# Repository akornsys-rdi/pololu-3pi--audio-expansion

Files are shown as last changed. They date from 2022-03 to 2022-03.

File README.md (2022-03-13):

# Pololu 3PI+ Audio Expansion API

Expansion board to provide audio playback for Pololu 3pi+ 32U4 Robot

## System interconnection diagram

            ┌──────┐   ┌──────┐         D    ┌───┐
            │ USB  │   │ USB  │       ┌──────┤RX │
            │SUBSYS│   │SUBSYS│       │      │ANT│
            ├──────┤   ├──────┤       ▼      └───┘
            ├──────┤ B ├──────┤   ┌──────┐
    ┌───┐   │      │◄──┤      │   │      │   ┌───┐
    │BAT├──►│ 32U4 │   │ SAMD │◄─►┤ TINY ├──►│RGB│
    │LVL│ A │      ├──►│      │ E │      │ D │LED│
    └───┘   ├──────┤ C ├──────┤   └──────┘   └───┘
            ├──────┤   ├──────┤       ▲
            │ROBOT │   │AUDIO │       │      ┌───┐
            │SUBSYS│   │SUBSYS│       └──────┤ID │
            └──────┘   └──────┘         A    │POT│
                                             └───┘
    COMMUNICATION:
    A -> ANALOG             B -> SERIAL DOWNLINK
    C -> SERIAL UPLINK      D -> DIGITAL PROTOCOL
    E -> DIGITAL INTERLINK

## Communication protocols

- Battery reading by analog reading of `A1` of the **ATmega32U4**, the `readBatteryMillivolts()` function (implemented by the Pololu library) provides this functionality.
- Reading the identifier selection potentiometer by analog reading of `A2` from the **ATtiny85**, the `readIdPot()` function (to be implemented in code) provides this functionality.
- Bidirectional communication between **ATmega32U4** and **ATSAMD21** via serial protocol with level shifting at 115200bps. The `Serial1` port is at the **ATmega32U4** end, while the `Serial` port is at the **ATSAMD21** end.
- Reading of the 433MHz radio receiver in 24bit protocol. Realized by the `rc-switch` library (fork).
- WS2812B type RGB LED writing. Realized by the `Adafruit NeoPixel` library.
- Communication primarily one-way from the **ATtiny85** to the **ATSAMD21**. The line level determines what has been received via the radio, leaving the line in high impedance (with pulldown) until the first reception. At startup, different pulses are generated to check the initial status and send the identifier (see corresponding sections).

## Software versions

**ATmega32U4**
- IDE: Arduino IDE 1.8.19
- Board: [Pololu A-Star Boards](https://github.com/pololu/a-star) 4.0.2 by Pololu
- Libraries: 
  + [Pololu3piPlus32U4](https://github.com/pololu/pololu-3pi-plus-32u4-arduino-library) 1.1.2 by Pololu
    * [FastGPIO](https://github.com/pololu/fastgpio-arduino) 2.1.0 by Pololu
    * [USBPause](https://github.com/pololu/usb-pause-arduino) 2.0.0 by Pololu
    * [Pushbutton](https://github.com/pololu/pushbutton-arduino) 2.0.0 by Pololu
    * [PololuBuzzer](https://github.com/pololu/pololu-buzzer-arduino) 1.2.0 by Pololu
    * [PololuHD44780](https://github.com/pololu/pololu-hd44780-arduino) 2.0.0 by Pololu
    * [PololuOLED](https://github.com/pololu/pololu-oled) 2.0.0 by Pololu
    * [PololuMenu](https://github.com/pololu/pololu-menu-arduino) 2.0.0 by Pololu
  + [TimerThree](https://playground.arduino.cc/Code/Timer1/) 1.1.0 by Jesse Tane, Jérôme Despatis, Michael Polli, Dan Clemens, Paul Stoffregen
  + [movingAvg](https://github.com/JChristensen/movingAvg) 2.3.1 by Jack Christensen

**ATSAMD21**
- IDE: Arduino IDE 1.8.19
- Board: Arduino SAMD Boards (32-bits ARM Cortex-M0+) 1.8.7 by Arduino
- Libraries:
  + [Arduino Sound](https://www.arduino.cc/en/Reference/ArduinoSound) 0.2.1 by Arduino
  + [SD](https://www.arduino.cc/en/Reference/SD) 1.2.3 by Arduino
  + [SDConfig](https://www.arduino.cc/reference/en/libraries/sdconfig/) 1.1.0 by Claus Mancini

**ATtiny85**
- IDE: Arduino IDE 1.8.19
- Board: [attiny](https://github.com/damellis/attiny) 1.0.2 by David A. Mellis
- Libreries: 
  + [Adafruit NeoPixel](https://github.com/adafruit/Adafruit_NeoPixel) 1.1.8 by Adafruit
  + [rc-switch](https://github.com/luelista/rc-switch/tree/feature-pcint-rebased) 2.6.2 by Mira Weller (fork).
    * [PinChangeInterrupt](https://github.com/NicoHood/PinChangeInterrupt) 1.2.9 by NicoHood
  + [ATtinySerialOut](https://github.com/ArminJo/ATtinySerialOut) 1.1.0 by Armin Joachimsmeyer

## General information

All **ATtiny85**, **ATSAMD21** and **ATmega32U4** firmware must share common values in the `N_ROBOTS` constant with the value of the maximum number of robots running simultaneously.

## Initial check

The **ATSAMD21** shall perform an initial check at startup, where it will check for the existence and correct access to the SD card, as well as that there is at least one valid audio of each required type. Hardware checks may also be performed. If any of these checks are not correct, the **ATSAMD21** will send the command `#` to the **ATmega32U4**, flash the user LED and, if available, attempt to play a special audio to indicate this circumstance. After this it will latch, ceasing to perform any other functionality until a power cycle is performed.

If the check is successful, it will send the `%` command, and will play, if available, an OK check audio. In the case of having the special audio of check ok, the command of this circumstance will be sent at the end of the reproduction of this audio. Once the initial check has been performed, the system will be able to perform the other functionalities explained in this document.

During the initial check at start-up of **ATSAMD21**, it will maintain the interlink line with **ATtiny85** at high level, thus indicating that it is present and that it is in the process of being checked. As soon as the initial check process is finished, this line will be set low and control of it will be given to the identifier assignment routine.

The **ATtiny85** can set a timeout time waiting for this high level signal, which if it does not appear, it will be considered that communication between these two microcontrollers cannot be established.

If the `MAIN.CFG` file is available on the SD card, it will try to read from it new settings, which will replace the default settings.

The **ATmega32U4** can set a timeout time, after which the Audio Expansion board is considered not available or does not respond. The behavior in this scenario is not determined.

## Identifier assignment operation

The assignment of the identifier is performed at system startup, when the potentiometer that selects the identifier is read. This reading by the **ATtiny85** is processed and converted into a range between `0` and `N_ROBOTS - 1`. The resulting `identifier` is transmitted by a variable width pulse to the **ATSAMD21**. Each identifier is assigned a color on the RGB LED by dividing the color spectrum by the constant `N_ROBOTS` and multiplying the hue angle by `identifier`.

For the pulse indicating the assigned identifier, the **ATSAMD21** after having performed its initial check (being successful), will generate a low level pause on the interlink line of 750µs. After this, it will generate a first high level pulse of 50µs, thus indicating to the **ATtiny85** that it is ready to receive. 5µs later, the **ATtiny85** starts a pulse with a length of (360µs/`N_ROBOTS`)*`identifier`. After this pulse it waits another 25µs at low level before giving control of the line to the remote command routine.

During program execution, the **ATtiny85** periodically reads the potentiometer that selects the identifier for changes. If a change is produced, it displays the new color corresponding to the resulting identifier for three seconds. This functionality has priority in the use of the RGB LED. The new identifier does not replace the previous one, and a power cycle is required for the new identifier selected via the potentiometer to be assigned.

In the communication between the **ATmega32U4** and the **ATSAMD21**, the former can ask at any time for the current identifier, by sending an `@`. If the **ATSAMD21** has already received the identifier from the **ATtiny85**, it will send a character between the `A` and the `~`. Otherwise, it will respond with `@`, thus indicating that it is still unknown. If this circumstance occurs, the **ATmega32U4** must keep asking until it gets a valid answer.

## Remote command operation

The remote command operation allows to pause the robots, or to resume running. It is performed through a 433MHz command, and the command received is processed by the **ATtiny85**. This command is relayed to the **ATSAMD21** via the interlink line level. The **ATSAMD21** will send a command to the **ATmega32U4** with each change of this command. At startup, until the first reception, it should be considered to be in a paused state.

The **ATtiny85** microcontroller decodes the keystroke received from the control and considers whether it is a pause or run command. The interlink line will be set to low or high level respectively. The line remains in high impedance state (with pulldown) until the first command is received.

The RGB LED will blink with the color of the identifier if paused, and will remain fixed for five seconds from the moment of activation, before turning off. It will turn back on with each change of command, remaining in the previous state if a keystroke equal to the current command is repeated.

At the moment of a new change detected by the **ATSAMD21**, it will generate a command via serial port to the **ATmega32U4**. A `&` is sent in case of a run resume command, and a `$` in case of pause or standby. The **ATmega32U4** must receive the command. No response is required.

## Audio playback operation

The **ATmega32U4** shall be able to generate audio playback and end of playback command at any time after the initial check. The **ATSAMD21** shall receive the command and act accordingly. There are two playback commands, depending on their type. The `>` command will initiate playback of path audios (type A), which will be repeated indefinitely if it reaches its end. The `!` command will start the playback of collision audios (type B), which will be played only once. The path audios will stop on receipt of the `=` command.

In the event of path audio playback, the **ATSAMD21** shall choose a random audio file among those provided on the SD card of its type, and start the playback. Randomly, between 1 and 5 times, the same path audio shall be played in successive receptions of that command, after which another audio shall be randomly chosen again with the same strategy.

In the event of collision audio playback, the **ATSAMD21** shall choose a random audio file among those provided on the SD card of its type, and start its playback until the file reaches its end.

If a play command is received while an audio file is already playing, this command will be ignored as long as a special audio is not being played, in which case it will be added to the play queue and played when the special audio is finished.

On the path audio playback stop event, the current audio playback will be stopped, as long as it is of this type. This action will do nothing if a file is not playing or if the playback is of another type.

### File format

The WAVE file format must be PCM mono 16bit at 22050Hz, with extension `.wav`. Any other format cannot be played.

### File names

For path and collision audios, only those files that are consecutive from `000` will be considered.

| File name | Type | Description |
|---|---|---|
| `A000.WAV` - `A999.WAV` | Required | Interval of path audios |
| `B000.WAV` - `B999.WAV` | Required | Interval of collision audios  |
| `CHKOK.WAV` | Special  | Initial check ok indicator |
| `CHKKO.WAV` | Special  | Initial check error indicator |
| `LWBAT.WAV` | Special  | Low battery indicator |

Special audios are optional.

## Battery readout operation

The battery level must be constantly monitored, in order to stop the robot if the charge drops below the `LOW_BATT` threshold. This monitoring is done by the **ATmega32U4**, which must send a command to the **ATSAMD21** in case the battery voltage drops below this threshold, which is done by sending a `-` only at the time of detection. The current battery comparison is done using the average of the last readings against the threshold.

This event should cause a latching event, and should not be recoverable until power is cycled. The **ATSAMD21** will play a special audio (if available) once to indicate low battery. If an audio is playing at the time the low battery command is received, the special audio will be retained and played after the previous one has finished. This event does not affect the playback of other audios, which must be stopped if explicitly required by the **ATmega32U4**.

## Debugging and LED status indication

The different LEDs located on the different boards of each robot have a meaning that can help to understand the current behavior of the robot, as well as to detect possible failures and their cause.

| LED | Lighting mode | Current status | Notes |
|---|---|---|---|
| Green LED on main board | 1Hz blinking | Waiting for identifier of **ATSAMD21** | |
| Yellow LED on main board | Fixed | Motion after obstacle detection or timeout | |
| Red LED on main board | 2Hz blinking | Low battery | |
| Green, yellow and red LEDs on main board | 10Hz blinking | Error in initial check | All LEDs simultaneously |
| Red LED on Audio Expansion board | Fixed | Battery charging | With USB connected to Audio Expansion |
| Red LED on Audio Expansion board | Off | Battery charged | With USB connected to Audio Expansion |
| Orange LED on Audio Expansion board | 31Hz blinking | SD card not found | No SD card |
| Orange LED on Audio Expansion board | 31Hz blinking | Audio files not found or not valid | With SD card |
| Orange LED on Audio Expansion board | Fixed | Playing audio | |
| RGB LED on Audio Expansion board | Fixed any color | Identifying color assigned to the robot | Right at startup |
| RGB LED on Audio Expansion board | 15Hz white blinking | Awaiting communication with **ATSAMD21** | In start-up sequence |
| RGB LED on Audio Expansion board | Fixed pure green | Successful communication with **ATSAMD21** | In start-up sequence after white blinking, duration 500ms |
| RGB LED on Audio Expansion board | Fixed pure red | Unsuccessful communication with **ATSAMD21** | In start-up sequence after white blinking, duration 500ms |
| RGB LED on Audio Expansion board | 8Hz robot identifier blinking | Pause mode | After the start-up sequence |
| RGB LED on Audio Expansion board | Fixed robot identifier | Active mode | After the start-up sequence, duration 5s |
| RGB LED on Audio Expansion board | Off | Active mode | After the start-up sequence, after being fixed for 5s |
| RGB LED on Audio Expansion board | Fixed any color | Identification color selection | After the start-up sequence, moving the identifier selection potentiometer or up to 3 seconds later |

## Summary of uplink/downlink commands

| Source | Destination | Command | Description |
|---|---|---|---|
| **ATSAMD21** | **ATmega32U4** | `#` | Initial check error |
| **ATSAMD21** | **ATmega32U4** | `%` | Initial check ok |
| **ATmega32U4** | **ATSAMD21** | `@` | Identifier request |
| **ATSAMD21** | **ATmega32U4** | `@` | Answer: Unknown identifier |
| **ATSAMD21** | **ATmega32U4** | `A` - `~` | Answer: Identifier number |
| **ATSAMD21** | **ATmega32U4** | `$` | Set pause mode |
| **ATSAMD21** | **ATmega32U4** | `&` | Set active mode |
| **ATmega32U4** | **ATSAMD21** | `>` | Start of path audio playback |
| **ATmega32U4** | **ATSAMD21** | `=` | Stop audio path playback |
| **ATmega32U4** | **ATSAMD21** | `!` | Start of collision audio playback |
| **ATmega32U4** | **ATSAMD21** | `-` | Low battery indicator |

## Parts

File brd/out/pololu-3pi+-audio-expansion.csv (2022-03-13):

Reference | Value | Footprint | Datasheet | Manufacturer | Manufacturer Part Number
U1 | ATSAMD21G18A-AUT | Package_QFP:TQFP-48_7x7mm_P0.5mm | lib/datasheets/ATSAM-D21.pdf | Microchip | ATSAMD21G18A-AU
U2 | MAX98357 | Package_DFN_QFN:QFN-16-1EP_3x3mm_P0.5mm_EP1.45x1.45mm_ThermalVias | lib/datasheets/MAX98357.pdf | Maxim Integrated | MAX98357AETE+T
C12 | 220pF | Capacitor_SMD:C_0805_2012Metric |  | Samsung Electro-Mechanics | CL21C221JBANNNC
J2 | Micro_SD_Card | 5009010801:5009010801 | lib/datasheets/5009010801.pdf | Molex | 500901-0801
Q1 | 2N7002 | Package_TO_SOT_SMD:SOT-23 | lib/datasheets/NX7002AK.pdf | Nexperia | NX7002AKVL
R2 | 10k | Resistor_SMD:R_0805_2012Metric |  | Bourns | CR0805-JW-103ELF
R4 | 10k | Resistor_SMD:R_0805_2012Metric |  | Bourns | CR0805-JW-103ELF
Q2 | 2N7002 | Package_TO_SOT_SMD:SOT-23 | lib/datasheets/NX7002AK.pdf | Nexperia | NX7002AKVL
R3 | 10k | Resistor_SMD:R_0805_2012Metric |  | Bourns | CR0805-JW-103ELF
R5 | 10k | Resistor_SMD:R_0805_2012Metric |  | Bourns | CR0805-JW-103ELF
SW1 | RESET | Button_Switch_SMD:SW_Push_SPST_NO_Alps_SKRK | lib/datasheets/PTS636.pdf | C&K Switches | PTS636 SP43 SMTR LFS
Y1 | 32.768kHz | Crystal:Crystal_SMD_3215-2Pin_3.2x1.5mm | lib/datasheets/FC-135.pdf | Epson | FC-135 32.7680KA-A5
C1 | 22pF | Capacitor_SMD:C_0805_2012Metric |  | Samsung Electro-Mechanics | CL21C220JBANFNC
C2 | 22pF | Capacitor_SMD:C_0805_2012Metric |  | Samsung Electro-Mechanics | CL21C220JBANFNC
R1 | 220R | Resistor_SMD:R_0805_2012Metric |  | Bourns | CR0805-JW-221ELF
D1 | ORANGE | LED_SMD:LED_0805_2012Metric | lib/datasheets/LO-R976.pdf | Osram | LO R976-PS-1-0-20-R18
C10 | 100nF | Capacitor_SMD:C_0805_2012Metric |  | Kemet | C0805C104M5RACTU
L1 | Choke | Inductor_SMD:L_0805_2012Metric | lib/datasheets/BKPxxxxxxxx.pdf | Taiyo Yuden | BKP2125HS331-T
LS1 | Speaker | Connector_PinHeader_2.54mm:PinHeader_1x02_P2.54mm_Horizontal | lib/datasheets/10129379.pdf | Amphenol | 10129379-902001BLF
L2 | Choke | Inductor_SMD:L_0805_2012Metric | lib/datasheets/BKPxxxxxxxx.pdf | Taiyo Yuden | BKP2125HS331-T
C13 | 220pF | Capacitor_SMD:C_0805_2012Metric |  | Samsung Electro-Mechanics | CL21C221JBANNNC
R6 | 100k | Resistor_SMD:R_0805_2012Metric |  | Yageo | RC0805FR-07100KL
C11 | 10µF | Capacitor_SMD:C_0805_2012Metric |  | Samsung Electro-Mechanics | CL21A106KOQNNNE
C4 | 100nF | Capacitor_SMD:C_0805_2012Metric |  | Kemet | C0805C104M5RACTU
C8 | 10µF | Capacitor_SMD:C_0805_2012Metric |  | Samsung Electro-Mechanics | CL21A106KOQNNNE
C9 | 100nF | Capacitor_SMD:C_0805_2012Metric |  | Kemet | C0805C104M5RACTU
C3 | 1µF | Capacitor_SMD:C_0805_2012Metric |  | Samsung Electro-Mechanics | CL21B105KAFNNNE
C5 | 100nF | Capacitor_SMD:C_0805_2012Metric |  | Kemet | C0805C104M5RACTU
C6 | 100nF | Capacitor_SMD:C_0805_2012Metric |  | Kemet | C0805C104M5RACTU
C7 | 100nF | Capacitor_SMD:C_0805_2012Metric |  | Kemet | C0805C104M5RACTU
J1 | JTAG | Connector_PinHeader_1.27mm:PinHeader_2x05_P1.27mm_Vertical_SMD | lib/datasheets/20021121.pdf | Amphenol | 20021121-00010D4LF
BT1 | 18650 | 18650-holder:18650-holder
J4 | VBAT | Connector_PinHeader_2.54mm:PinHeader_1x02_P2.54mm_Vertical | lib/datasheets/10129378.pdf | Amphenol | 10129378-902003BLF
J5 | SWITCH | Connector_PinHeader_2.54mm:PinHeader_1x02_P2.54mm_Vertical | lib/datasheets/10129378.pdf | Amphenol | 10129378-902003BLF
U3 | MCP73831-2-OT | Package_TO_SOT_SMD:SOT-23-5 | lib/datasheets/MCP73831.pdf | Microchip | MCP73831T-2ACI/OT
J3 | USB_B_Mini | Connector_USB:USB_Mini-B_Wuerth_65100516121_Horizontal | lib/datasheets/UJ2-MBH.pdf | CUI Devices | UJ2-MBH-1-SMT-TR
J6 | POWER | Connector_PinHeader_2.54mm:PinHeader_2x03_P2.54mm_Vertical_SMD | lib/datasheets/10129383.pdf | Amphenol | 10129383-906002BLF
C14 | 4.7nF | Capacitor_SMD:C_0805_2012Metric |  | Kemet | C0805C472K5RACTU
R7 | 1M | Resistor_SMD:R_0805_2012Metric |  | Bourns | CR0805-FX-1004ELF
R9 | 1k | Resistor_SMD:R_0805_2012Metric |  | Bourns | CR0805-JW-102ELF
D3 | RED | LED_SMD:LED_0805_2012Metric | lib/datasheets/AP2012SRCPRV.pdf | Kingbright | AP2012SRCPRV
F1 | 750mA | Fuse:Fuse_1206_3216Metric | lib/datasheets/0ZCJ_series.pdf | Bel | 0ZCJ0075AF2E
BT2 | 18650 | 18650-holder:18650-holder
F2 | 750mA | Fuse:Fuse_1206_3216Metric | lib/datasheets/0ZCJ_series.pdf | Bel | 0ZCJ0075AF2E
R8 | 2k | Resistor_SMD:R_0805_2012Metric |  | Bourns | CR0805-JW-202ELF
SW2 | LATCH | Button_Switch_SMD:SW_SPST_B3U-3000P | lib/datasheets/SKRTLAE010.pdf | Alps Alpine | SKRTLAE010
J7 | EXP | Connector_PinHeader_2.54mm:PinHeader_2x03_P2.54mm_Vertical_SMD | lib/datasheets/10129383.pdf | Amphenol | 10129383-906002BLF
D2 | STF202-22T1G | Package_SO:TSOP-6_1.65x3.05mm_P0.95mm | lib/datasheets/STF202.pdf | OnSemi | STF202-22T1G
C16 | 10µF | Capacitor_SMD:C_0805_2012Metric |  | Samsung Electro-Mechanics | CL21A106KOQNNNE
C15 | 10µF | Capacitor_SMD:C_0805_2012Metric |  | Samsung Electro-Mechanics | CL21A106KOQNNNE
C17 | 150µF | Capacitor_Tantalum_SMD:CP_EIA-6032-20_AVX-F |  | AVX | TAJC157M010RNJ
C18 | 47µF | Capacitor_Tantalum_SMD:CP_EIA-3528-15_AVX-H |  | AVX | TAJB476K006RNJ
U4 | ATtiny85-20SU | Package_SO:SOIJ-8_5.3x5.3mm_P1.27mm | lib/datasheets/ATtiny85.pdf | Microchip | ATTINY85-20SU
D4 | WS2812B | LED_SMD:LED_WS2812B_PLCC4_5.0x5.0mm_P3.2mm | lib/datasheets/WS2812B.pdf | Worldsemi | WS2812B
J9 | RX_MODULE | Connector_PinSocket_2.54mm:PinSocket_1x04_P2.54mm_Vertical
C19 | 100nF | Capacitor_SMD:C_0805_2012Metric |  | Kemet | C0805C104M5RACTU
R12 | 1k | Resistor_SMD:R_0805_2012Metric |  | Bourns | CR0805-JW-102ELF
R11 | 10k | Potentiometer_SMD:Potentiometer_Bourns_3269W_Vertical | lib/datasheets/3361.pdf | Bourns | 3361P-1-103GLF
J8 | ISP | Connector_IDC:IDC-Header_2x03_P2.54mm_Vertical
R10 | 10k | Resistor_SMD:R_0805_2012Metric |  | Bourns | CR0805-JW-103ELF
Q3 | 2N7002 | Package_TO_SOT_SMD:SOT-23 | lib/datasheets/NX7002AK.pdf | Nexperia | NX7002AKVL
R15 | 10k | Resistor_SMD:R_0805_2012Metric |  | Bourns | CR0805-JW-103ELF
R16 | 10k | Resistor_SMD:R_0805_2012Metric |  | Bourns | CR0805-JW-103ELF
R13 | 1k | Resistor_SMD:R_0805_2012Metric |  | Bourns | CR0805-JW-102ELF
C20 | 10µF | Capacitor_SMD:C_0805_2012Metric |  | Samsung Electro-Mechanics | CL21A106KOQNNNE
R14 | 100k | Resistor_SMD:R_0805_2012Metric |  | Yageo | RC0805FR-07100KL

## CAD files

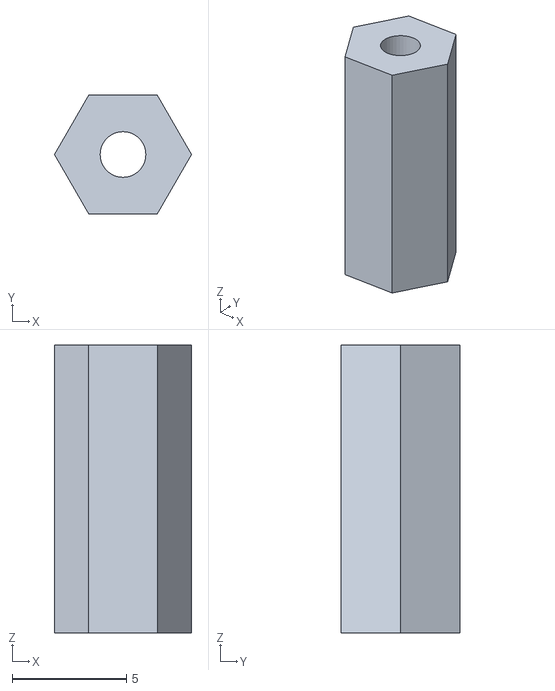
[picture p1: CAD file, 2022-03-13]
3d/spacers/spacer_small.stl
6.00 x 5.20 x 12.6

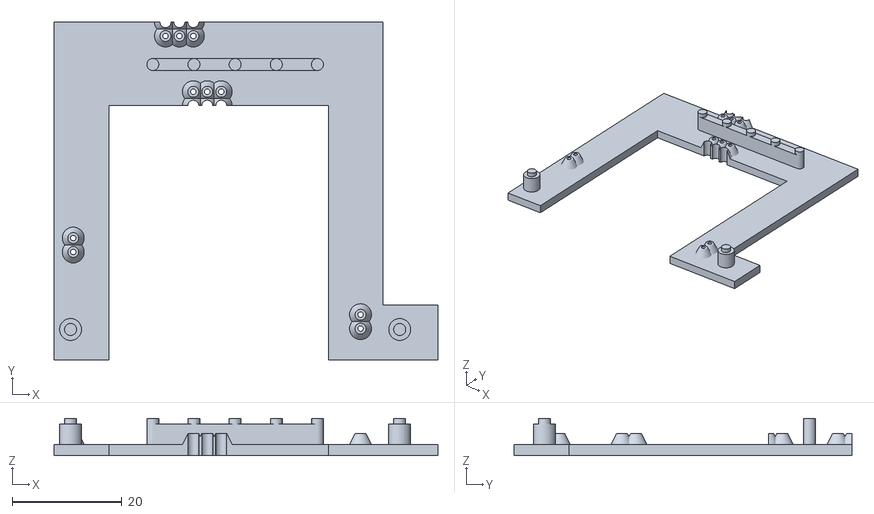
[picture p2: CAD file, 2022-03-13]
3d/stencil/stencil.stl
70.0 x 61.6 x 6.75

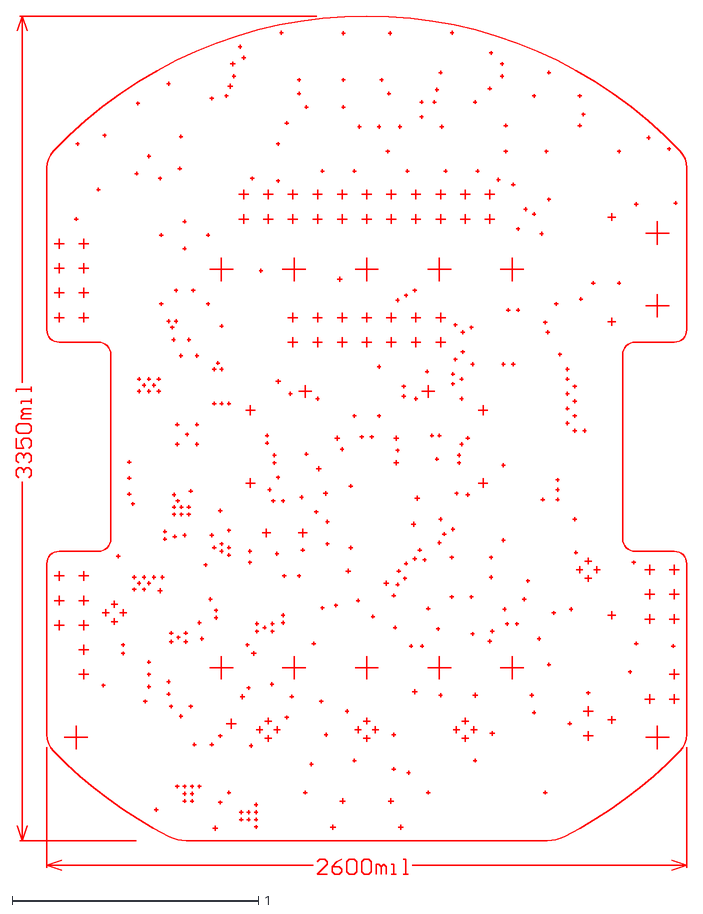
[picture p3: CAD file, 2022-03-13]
doc/3pi03a-drill.dxf
2.72 x 3.49

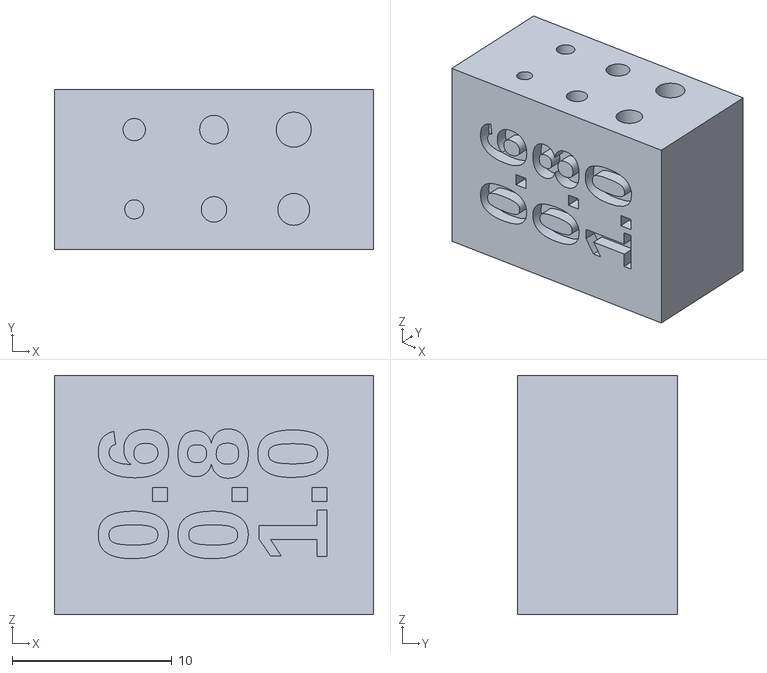
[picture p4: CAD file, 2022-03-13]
3d/spacers/drill_sizes.stl
20.0 x 10.0 x 15.0

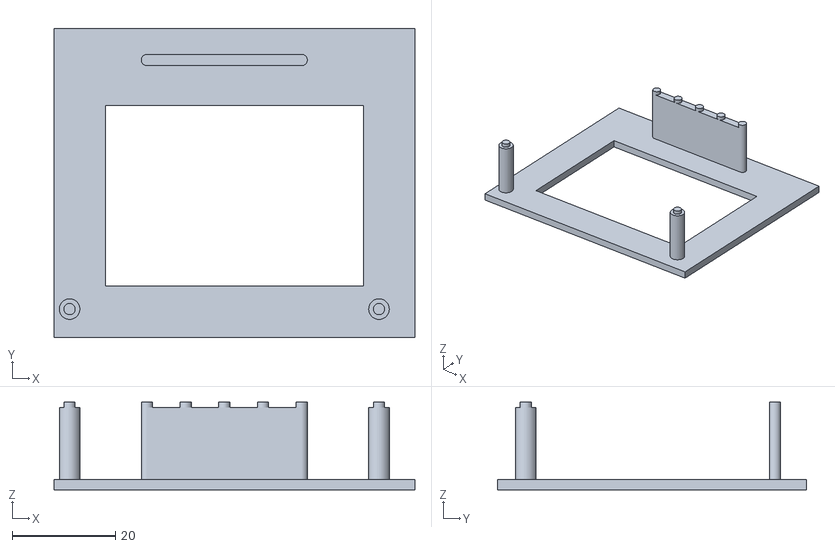
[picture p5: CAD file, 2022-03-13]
3d/stencil/support.stl
70.0 x 60.0 x 17.0

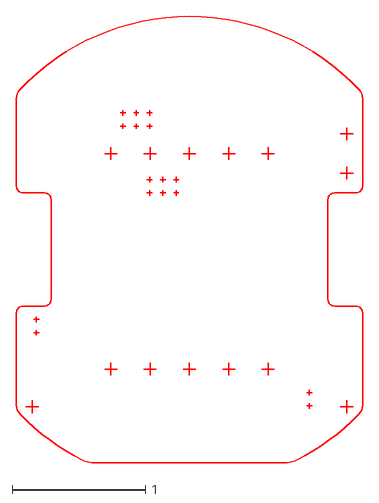
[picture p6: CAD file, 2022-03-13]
doc/3pi03a-drill-cleaned.dxf
2.60 x 3.35

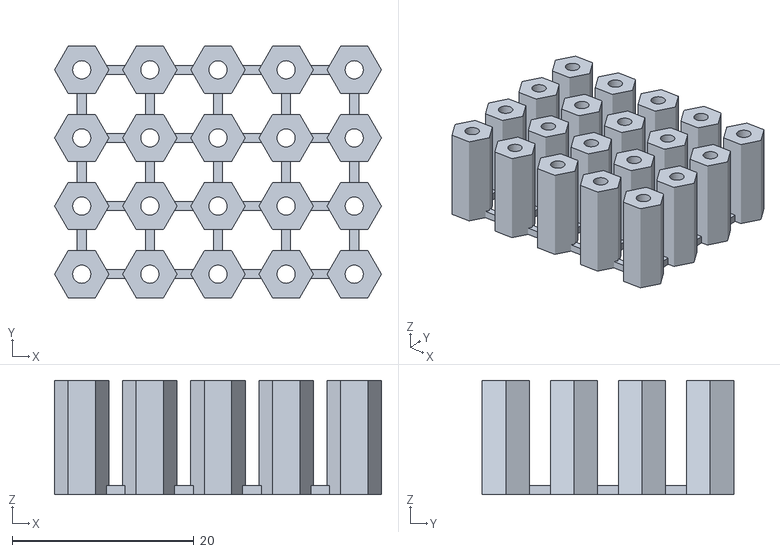
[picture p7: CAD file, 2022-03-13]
3d/spacers/spacer_small_matrix.stl
36.0 x 27.7 x 12.6

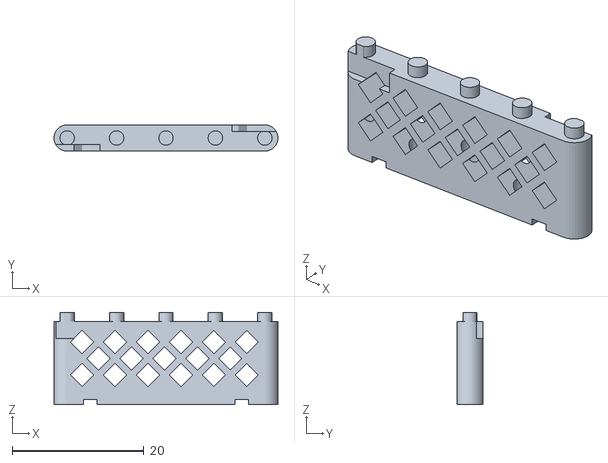
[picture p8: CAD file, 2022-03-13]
3d/spacers/spacer_big.stl
34.0 x 4.00 x 14.0

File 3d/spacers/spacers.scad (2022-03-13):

$fn=36;

*spacer_small_matrix();
*spacer_big_matrix();

*drill_sizes();
*spacer_big();
*spacer_small();

module spacer_small_matrix() {
    grid=7.5;
    for(x=[0:grid:(grid*4)]) {
        for(y=[0:grid:(grid*3)]) {
            translate([x,y,0]) spacer_small();
        }
    }
    for(x=[0:grid:(grid*4)]) {
        for(y=[0:grid:grid*2]) {
            translate([x-0.5,y+1,0]) cube([1,grid-2,,1]);
        }
    }
    for(x=[0:grid:(grid*3)]) {
        for(y=[0:grid:(grid*3)]) {
            translate([x+1,y-0.5,0]) cube([grid-2,1,1]);
        }
    }
}

module spacer_big_matrix() {
    gridx=35;
    gridy=5;
    for(x=[0:gridx:gridx]) {
        for(y=[0:gridy:(gridy*5)]) {
            translate([x,y,0]) spacer_big();
        }
    }
    for(x=[0:gridx:gridx]) {
        for(y=[0:gridy:(gridy*4)]) {
            translate([x+15,y+1,0]) cube([1,gridy-2,,1]);
        }
    }
    for(x=[0:gridx:gridx-1]) {
        for(y=[0:gridy:(gridy*5)]) {
            translate([x+31.5,y-0.5,0]) cube([gridx-33,1,1]);
        }
    }
}

module spacer_small() {
    difference() {
        union() {
            cylinder(r=3, h=12.6, $fn=6);
        }
        union() {
            translate([0,0,-1]) cylinder(r=1, h=15);
        }
    }
}

module spacer_big() {
    difference() {
        union() {
            hull() {
                cylinder(r=2, h=12.6);
                translate([30.00248,0,0]) cylinder(r=2, h=12.6);
            }
            for(i = [0:7.50062:(7.50062*4)]) {
                translate([i,0,0]) cylinder(r=1.1, h=12.6+1.4);
            }
        }
        union() {
            for(i = [0:(7.50062):(7.50062*4)]) {
                translate([i,0,-1]) cylinder(r=1, h=8);
            }
            for(i = [3.5-1, (7.50062*4)-3.5-1]) {
                translate([i,-3,-1]) cube([2,6,1.8]);
            }
            translate([7.50062*2,0,0]) for(i = [0,180]) {
                rotate([0,0,i]) translate([-17,-3,10]) cube([7,2,5]);
            }
            for(x = [0.5:5:26]) {
                for(z = [4.5:5:10]) {
                    translate([x,-3,z]) rotate([0,45,0]) cube([2.5,6,2.5]);
                }
            }
            for(x = [3:5:25]) {
                translate([x,-3,7]) rotate([0,45,0]) cube([2.5,6,2.5]);
            }
        }
    }
}

module drill_sizes() {
    difference() {
        cube([20,10,15]);
        translate([5,2.5,10]) cylinder(r=0.6, h=6);
        translate([5,7.5,10]) cylinder(r=0.7, h=6);
        translate([10,2.5,10]) cylinder(r=0.8, h=6);
        translate([10,7.5,10]) cylinder(r=0.9, h=6);
        translate([15,2.5,10]) cylinder(r=1, h=6);
        translate([15,7.5,10]) cylinder(r=1.1, h=6);
        translate([10,5,-1]) mirror([1,0,0]) linear_extrude(2) text("PETG", font=":bold", size=5, valign="center", halign="center");
        translate([5,1,7.5]) rotate([90,-90,0]) linear_extrude(2) text("0.6", font=":bold", size=4.5, valign="center", halign="center");
        translate([10,1,7.5]) rotate([90,-90,0]) linear_extrude(2) text("0.8", font=":bold", size=4.5, valign="center", halign="center");
        translate([15,1,7.5]) rotate([90,-90,0]) linear_extrude(2) text("1.0", font=":bold", size=4.5, valign="center", halign="center");
        translate([5,9,7.5]) rotate([-90,-90,0]) linear_extrude(2) text("0.7", font=":bold", size=4.5, valign="center", halign="center");
        translate([10,9,7.5]) rotate([-90,-90,0]) linear_extrude(2) text("0.9", font=":bold", size=4.5, valign="center", halign="center");
        translate([15,9,7.5]) rotate([-90,-90,0]) linear_extrude(2) text("1.1", font=":bold", size=4.5, valign="center", halign="center");
    }
}

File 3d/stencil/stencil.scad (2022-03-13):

$fn=36;

*stencil();
*support();

module support() {
    difference() {
        union() {
            cube([70,60,2]);
            translate([18.01876,80-26.1493,2]) hull() {
                cylinder(r=1.1, h=14);
                translate([(48.02124-18.01876),0,0]) cylinder(r=1.1, h=14);
            }
            translate([18.01876,80-26.1493,2]) cylinder(r=1.1, h=14+1);
            translate([25.51938,80-26.1493,2]) cylinder(r=1.1, h=14+1);
            translate([33.02,80-26.1493,2]) cylinder(r=1.1, h=14+1);
            translate([40.52062,80-26.1493,2]) cylinder(r=1.1, h=14+1);
            translate([48.02124,80-26.1493,2]) cylinder(r=1.1, h=14+1);
            translate([63.01994,80-74.44994,2]) cylinder(r=2, h=14);
            translate([63.01994,80-74.44994,2]) cylinder(r=1.1, h=14+1);
            translate([3.02006,80-74.44994,2]) cylinder(r=2, h=14);
            translate([3.02006,80-74.44994,2]) cylinder(r=1.1, h=14+1);
        }
        translate([10,10,-2]) cube([50,35,6]);
    }
}

module stencil() {
    difference() {
        union() {
            cube([70,80,2]);
            translate([3.51,80-57.785,2]) support_1x2();
            translate([55.88,80-71.755,2]) support_1x2();
            translate([27.94,80-32.385,2]) support_2x3();
            translate([22.86,80-19.685,2]) support_2x3();
            union() {
                translate([18.01876,80-26.1493,2]) hull() {
                    cylinder(r=1.1, h=3.75);
                    translate([(48.02124-18.01876),0,0]) cylinder(r=1.1, h=3.75);
                }
                translate([18.01876,80-26.1493,2]) cylinder(r=1.1, h=3.75+1);
                translate([25.51938,80-26.1493,2]) cylinder(r=1.1, h=3.75+1);
                translate([33.02,80-26.1493,2]) cylinder(r=1.1, h=3.75+1);
                translate([40.52062,80-26.1493,2]) cylinder(r=1.1, h=3.75+1);
                translate([48.02124,80-26.1493,2]) cylinder(r=1.1, h=3.75+1);
                translate([63.01994,80-74.44994,2]) cylinder(r=2, h=3.75);
                translate([63.01994,80-74.44994,2]) cylinder(r=1.1, h=3.75+1);
                translate([3.02006,80-74.44994,2]) cylinder(r=2, h=3.75);
                translate([3.02006,80-74.44994,2]) cylinder(r=1.1, h=3.75+1);
            }
        }
        union() {
            union() {
                translate([3.51,80-57.785,-1]) conn_1x2();
                translate([55.88,80-71.755,-1]) conn_1x2();
                translate([27.94,80-32.385,-1]) rotate([0,0,180]) conn_2x3();
                translate([22.86,80-19.685,-1]) conn_2x3();
            }
            union() {
                translate([10,-1,-1]) cube([40,40,6]);
                translate([60,10,-1]) cube([11,55,6]);
                translate([10,80-32.385+1.27-2.54-8,-1]) cube([40,8,6]);
                translate([-1,80-19.685+1.27,-1]) cube([72,20,6]);
            }
        }
    }
}

module support_1x2() {
    cylinder(r1=2, r2=1, h=2);
    translate([0,-2.54,0]) cylinder(r1=2, r2=1, h=2);
}

module support_2x3() {
    translate([-2.54,1.27,0]) union() {
        cylinder(r1=2, r2=1, h=2);
        translate([2.54,0,0]) cylinder(r1=2, r2=1, h=2);
        translate([5.08,0,0]) cylinder(r1=2, r2=1, h=2);
        translate([0,-2.54,0]) cylinder(r1=2, r2=1, h=2);
        translate([2.54,-2.54,0]) cylinder(r1=2, r2=1, h=2);
        translate([5.08,-2.54,0]) cylinder(r1=2, r2=1, h=2);
    }
}

module conn_1x2() {
    cylinder(r=0.5, h=6);
    translate([0,-2.54,0]) cylinder(r=0.5, h=6);
}

module conn_2x3() {
    translate([-2.54,1.27,0]) union() {
        cylinder(r=1, h=6);
        translate([2.54,0,0]) cylinder(r=1, h=6);
        translate([5.08,0,0]) cylinder(r=1, h=6);
        translate([0,-2.54,0]) cylinder(r=0.5, h=6);
        translate([2.54,-2.54,0]) cylinder(r=0.5, h=6);
        translate([5.08,-2.54,0]) cylinder(r=0.5, h=6);
    }
}

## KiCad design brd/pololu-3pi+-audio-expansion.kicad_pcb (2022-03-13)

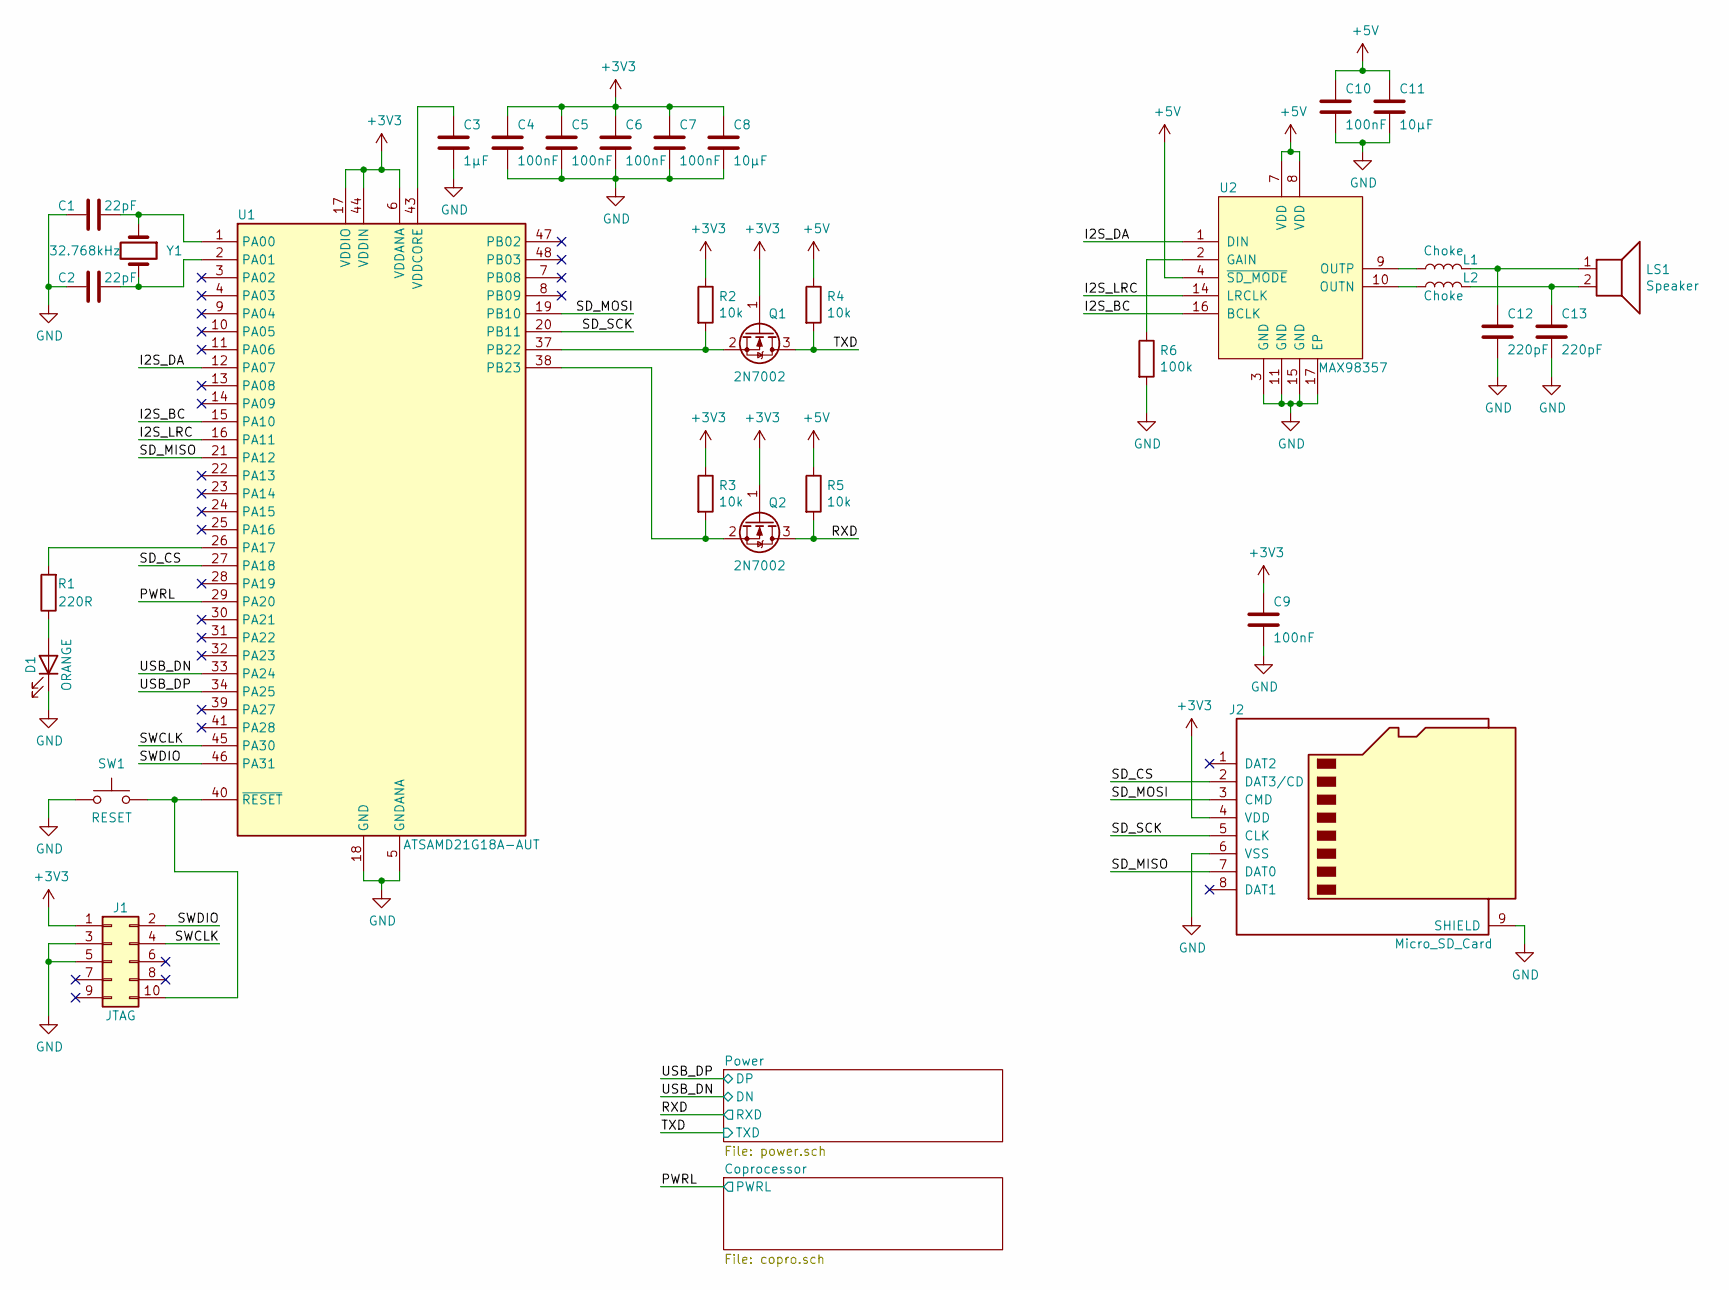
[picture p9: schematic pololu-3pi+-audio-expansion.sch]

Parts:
C1, C2: 22pF; C_0805_2012Metric; Manufacturer Part Number CL21C220JBANFNC
C3: 1µF; C_0805_2012Metric; Manufacturer Part Number CL21B105KAFNNNE
C4, C5, C6, C7, C9, C10: 100nF; C_0805_2012Metric; Manufacturer Part Number C0805C104M5RACTU
C8, C11: 10µF; C_0805_2012Metric; Manufacturer Part Number CL21A106KOQNNNE
C12, C13: 220pF; C_0805_2012Metric; Manufacturer Part Number CL21C221JBANNNC
D1: ORANGE; LED_0805_2012Metric; Manufacturer Part Number LO R976-PS-1-0-20-R18
J1: JTAG; PinHeader_2x05_P1.27mm_Vertical_SMD; Manufacturer Part Number 20021121-00010D4LF
J2: Micro_SD_Card; 5009010801; Manufacturer Part Number 500901-0801
L1, L2: Choke; L_0805_2012Metric; Manufacturer Part Number BKP2125HS331-T
LS1: Speaker; PinHeader_1x02_P2.54mm_Horizontal; Manufacturer Part Number 10129379-902001BLF
Q1, Q2: 2N7002; SOT-23; Manufacturer Part Number NX7002AKVL
R1: 220R; R_0805_2012Metric; Manufacturer Part Number CR0805-JW-221ELF
R2, R3, R4, R5: 10k; R_0805_2012Metric; Manufacturer Part Number CR0805-JW-103ELF
R6: 100k; R_0805_2012Metric; Manufacturer Part Number RC0805FR-07100KL
SW1: RESET; SW_Push_SPST_NO_Alps_SKRK; Manufacturer Part Number PTS636 SP43 SMTR LFS
U1: ATSAMD21G18A-AUT; TQFP-48_7x7mm_P0.5mm; Manufacturer Part Number ATSAMD21G18A-AU
U2: MAX98357; QFN-16-1EP_3x3mm_P0.5mm_EP1.45x1.45mm_ThermalVias; Manufacturer Part Number MAX98357AETE+T
Y1: 32.768kHz; Crystal_SMD_3215-2Pin_3.2x1.5mm; Manufacturer Part Number FC-135 32.7680KA-A5

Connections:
+3V3: C4.1, C5.1, C6.1, C7.1, C8.1, C9.1, J1.1, J2.4 (VDD), Q1.1 (G), Q2.1 (G), R2.1, R3.1, U1.6 (VDDANA), U1.17 (VDDIO), U1.36 (VDDIO), U1.44 (VDDIN); also elsewhere on the board
+5V: C10.1, C11.1, R4.1, R5.1, U2.4 (~SD_MODE), U2.7 (VDD), U2.8 (VDD); also elsewhere on the board
/I2S_BC: U1.15 (PA10), U2.16 (BCLK)
/I2S_DA: U1.12 (PA07), U2.1 (DIN)
/I2S_LRC: U1.16 (PA11), U2.14 (LRCLK)
/PWRL: U1.29 (PA20); also elsewhere on the board
/RXD: Q2.3 (D), R5.2; also elsewhere on the board
/SD_CS: J2.2 (DAT3/CD), U1.27 (PA18)
/SD_MISO: J2.7 (DAT0), U1.21 (PA12)
/SD_MOSI: J2.3 (CMD), U1.19 (PB10)
/SD_SCK: J2.5 (CLK), U1.20 (PB11)
/SWCLK: J1.4, U1.45 (PA30)
/SWDIO: J1.2, U1.46 (PA31)
/TXD: Q1.3 (D), R4.2; also elsewhere on the board
/USB_DN: U1.33 (PA24); also elsewhere on the board
/USB_DP: U1.34 (PA25); also elsewhere on the board
GND: C1.2, C2.2, C3.2, C4.2, C5.2, C6.2, C7.2, C8.2, C9.2, C10.2, C11.2, C12.2, C13.2, D1.1 (K), J1.3, J1.5, J2.6 (VSS), J2.9 (SHIELD), R6.2, SW1.1, U1.5 (GNDANA), U1.18 (GND), U1.35 (GND), U1.42 (GND), U2.3 (GND), U2.11 (GND), U2.15 (GND), U2.17 (EP); also elsewhere on the board
unnamed: C1.1, U1.1 (PA00), Y1.1
unnamed: C2.1, U1.2 (PA01), Y1.2
unnamed: C3.1, U1.43 (VDDCORE)
unnamed: C12.1, L1.2, LS1.1
unnamed: C13.1, L2.2, LS1.2
unnamed: D1.2 (A), R1.1
unnamed: J1.10, SW1.2, U1.40 (~RESET)
unnamed: L1.1, U2.9 (OUTP)
unnamed: L2.1, U2.10 (OUTN)
unnamed: Q1.2 (S), R2.2, U1.37 (PB22)
unnamed: Q2.2 (S), R3.2, U1.38 (PB23)
unnamed: R1.2, U1.26 (PA17)
unnamed: R6.1, U2.2 (GAIN)

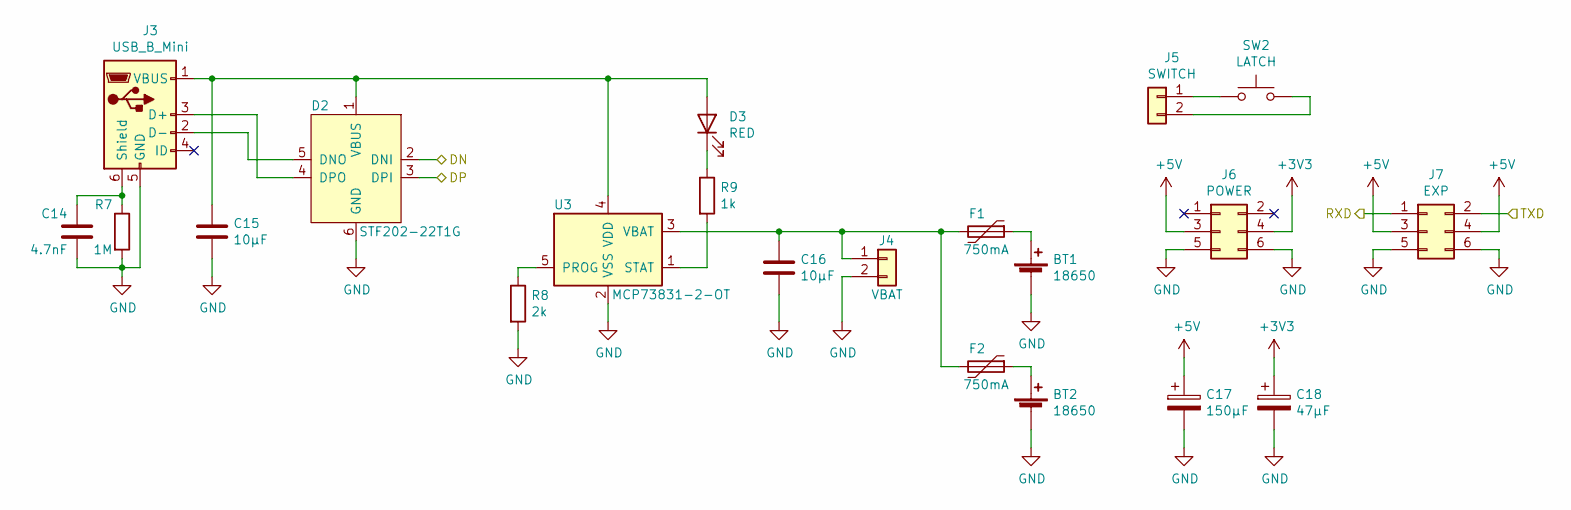
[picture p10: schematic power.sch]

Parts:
BT1, BT2: 18650; 18650-holder
C14: 4.7nF; C_0805_2012Metric; Manufacturer Part Number C0805C472K5RACTU
C15, C16: 10µF; C_0805_2012Metric; Manufacturer Part Number CL21A106KOQNNNE
C17: 150µF; CP_EIA-6032-20_AVX-F; Manufacturer Part Number TAJC157M010RNJ
C18: 47µF; CP_EIA-3528-15_AVX-H; Manufacturer Part Number TAJB476K006RNJ
D2: STF202-22T1G; TSOP-6_1.65x3.05mm_P0.95mm; Manufacturer Part Number STF202-22T1G
D3: RED; LED_0805_2012Metric; Manufacturer Part Number AP2012SRCPRV
F1, F2: 750mA; Fuse_1206_3216Metric; Manufacturer Part Number 0ZCJ0075AF2E
J3: USB_B_Mini; USB_Mini-B_Wuerth_65100516121_Horizontal; Manufacturer Part Number UJ2-MBH-1-SMT-TR
J4: VBAT; PinHeader_1x02_P2.54mm_Vertical; Manufacturer Part Number 10129378-902003BLF
J5: SWITCH; PinHeader_1x02_P2.54mm_Vertical; Manufacturer Part Number 10129378-902003BLF
J6: POWER; PinHeader_2x03_P2.54mm_Vertical_SMD; Manufacturer Part Number 10129383-906002BLF
J7: EXP; PinHeader_2x03_P2.54mm_Vertical_SMD; Manufacturer Part Number 10129383-906002BLF
R7: 1M; R_0805_2012Metric; Manufacturer Part Number CR0805-FX-1004ELF
R8: 2k; R_0805_2012Metric; Manufacturer Part Number CR0805-JW-202ELF
R9: 1k; R_0805_2012Metric; Manufacturer Part Number CR0805-JW-102ELF
SW2: LATCH; SW_SPST_B3U-3000P; Manufacturer Part Number SKRTLAE010
U3: MCP73831-2-OT; SOT-23-5; Manufacturer Part Number MCP73831T-2ACI/OT

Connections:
+3V3: C18.1, J6.4; also elsewhere on the board
+5V: C17.1, J6.3, J7.3, J7.4; also elsewhere on the board
/RXD: J7.1; also elsewhere on the board
/TXD: J7.2; also elsewhere on the board
/USB_DN: D2.2 (DNI); also elsewhere on the board
/USB_DP: D2.3 (DPI); also elsewhere on the board
GND: BT1.2 (-), BT2.2 (-), C14.2, C15.2, C16.2, C17.2, C18.2, D2.6 (GND), J3.5 (GND), J4.2, J6.5, J6.6, J7.5, J7.6, R7.2, R8.2, U3.2 (VSS); also elsewhere on the board
unnamed: BT1.1 (+), F1.1
unnamed: BT2.1 (+), F2.1
unnamed: C14.1, J3.6 (Shield), R7.1
unnamed: C15.1, D2.1 (VBUS), D3.2 (A), J3.1 (VBUS), U3.4 (VDD)
unnamed: C16.1, F1.2, F2.2, J4.1, U3.3 (VBAT)
unnamed: D2.4 (DPO), J3.3 (D+)
unnamed: D2.5 (DNO), J3.2 (D-)
unnamed: D3.1 (K), R9.1
unnamed: J5.1, SW2.1
unnamed: J5.2, SW2.2
unnamed: R8.1, U3.5 (PROG)
unnamed: R9.2, U3.1 (STAT)

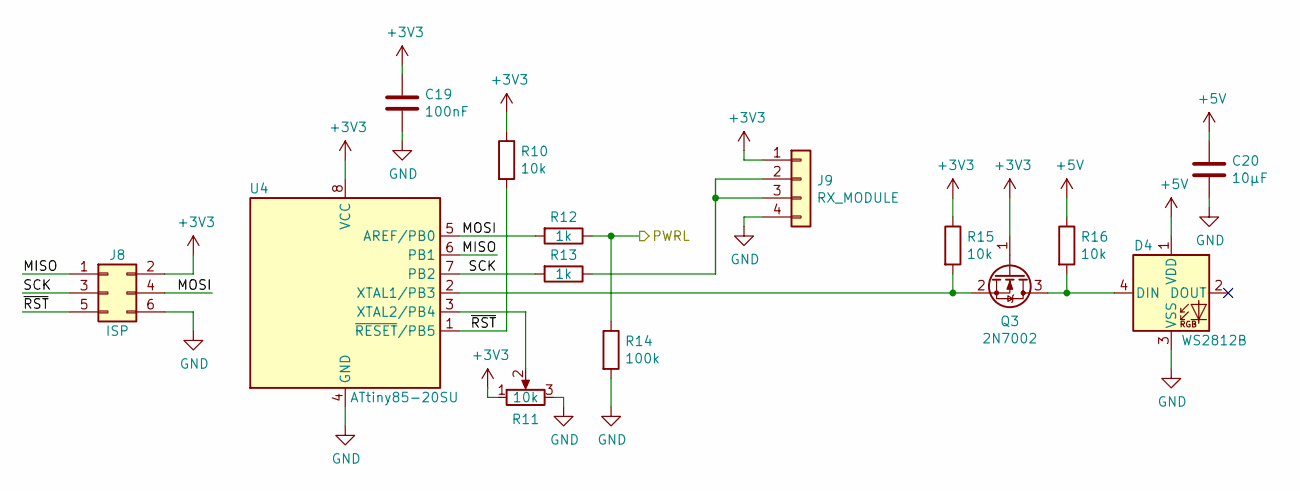
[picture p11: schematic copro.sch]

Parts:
C19: 100nF; C_0805_2012Metric; Manufacturer Part Number C0805C104M5RACTU
C20: 10µF; C_0805_2012Metric; Manufacturer Part Number CL21A106KOQNNNE
D4: WS2812B; LED_WS2812B_PLCC4_5.0x5.0mm_P3.2mm; Manufacturer Part Number WS2812B
J8: ISP; IDC-Header_2x03_P2.54mm_Vertical
J9: RX_MODULE; PinSocket_1x04_P2.54mm_Vertical
Q3: 2N7002; SOT-23; Manufacturer Part Number NX7002AKVL
R10, R15, R16: 10k; R_0805_2012Metric; Manufacturer Part Number CR0805-JW-103ELF
R11: 10k; Potentiometer_Bourns_3269W_Vertical; Manufacturer Part Number 3361P-1-103GLF
R12, R13: 1k; R_0805_2012Metric; Manufacturer Part Number CR0805-JW-102ELF
R14: 100k; R_0805_2012Metric; Manufacturer Part Number RC0805FR-07100KL
U4: ATtiny85-20SU; SOIJ-8_5.3x5.3mm_P1.27mm; Manufacturer Part Number ATTINY85-20SU

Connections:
+3V3: C19.1, J8.2, J9.1, Q3.1 (G), R10.1, R11.1, R15.1, U4.8 (VCC); also elsewhere on the board
+5V: C20.1, D4.1 (VDD), R16.1; also elsewhere on the board
/Coprocessor/MISO: J8.1, U4.6 (PB1)
/Coprocessor/MOSI: J8.4, R12.2, U4.5 (AREF/PB0)
/Coprocessor/SCK: J8.3, R13.2, U4.7 (PB2)
/Coprocessor/~RST: J8.5, R10.2, U4.1 (~RESET~/PB5)
/PWRL: R12.1, R14.1; also elsewhere on the board
GND: C19.2, C20.2, D4.3 (VSS), J8.6, J9.4, R11.3, R14.2, U4.4 (GND); also elsewhere on the board
unnamed: D4.4 (DIN), Q3.3 (D), R16.2
unnamed: J9.2, J9.3, R13.1
unnamed: Q3.2 (S), R15.2, U4.2 (XTAL1/PB3)
unnamed: R11.2, U4.3 (XTAL2/PB4)

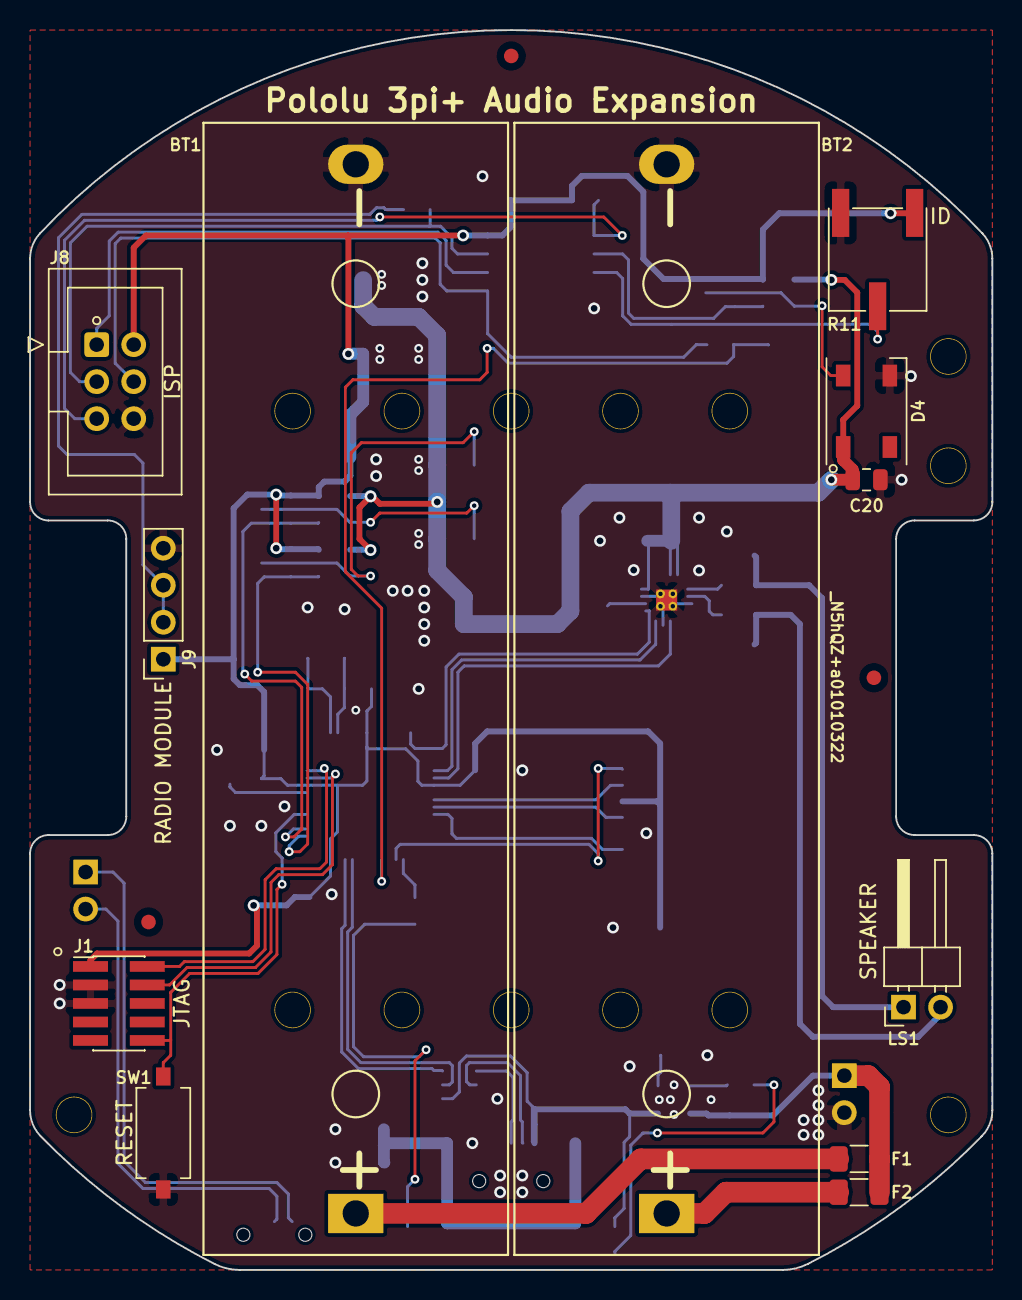
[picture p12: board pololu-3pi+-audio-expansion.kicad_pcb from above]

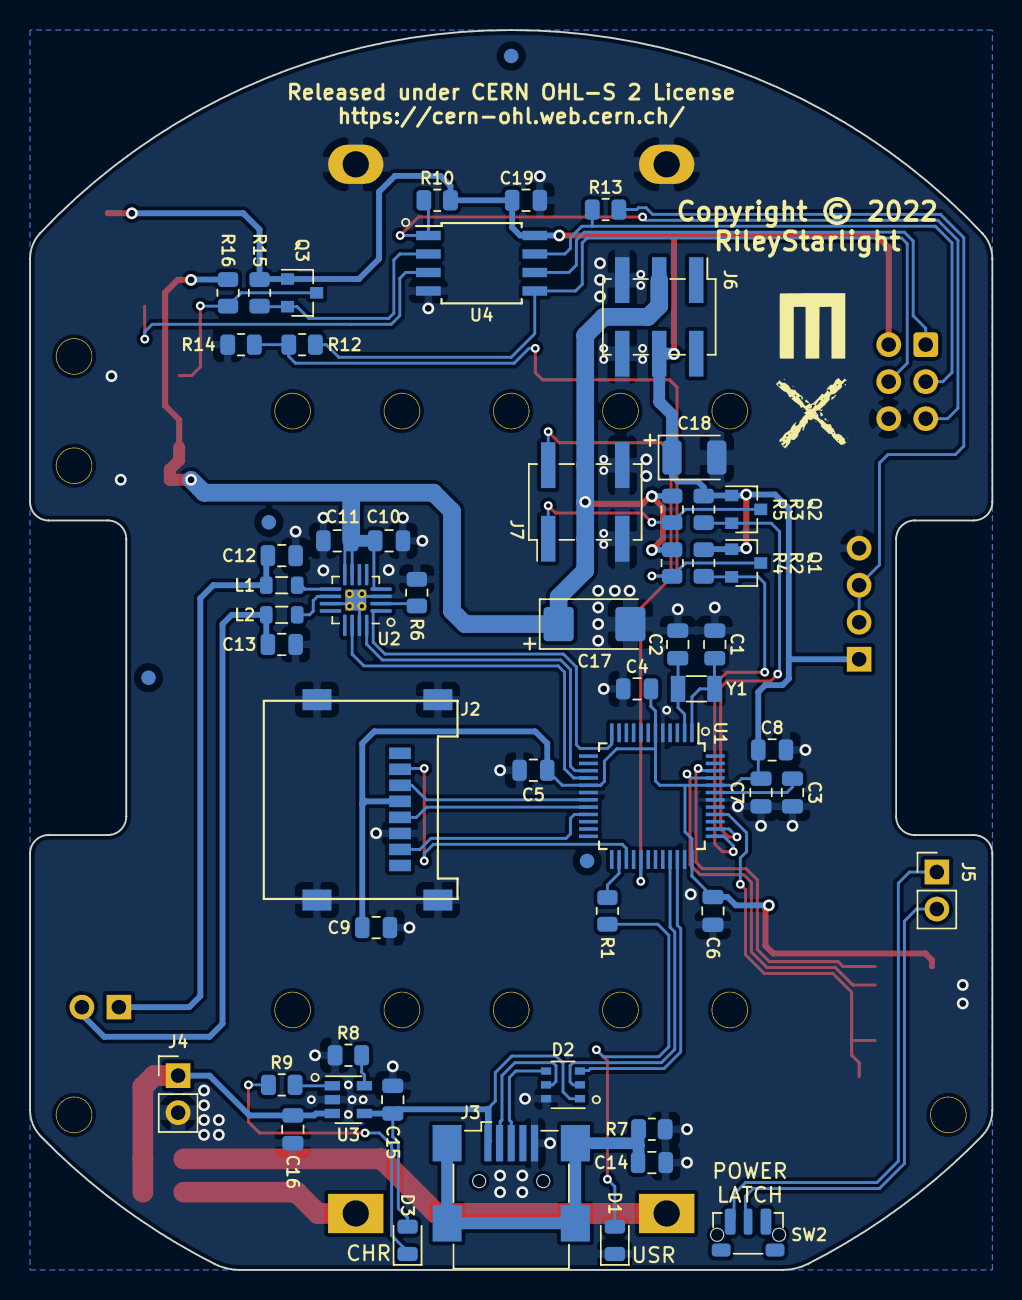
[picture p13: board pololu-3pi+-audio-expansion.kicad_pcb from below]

Board: 2 copper layers, 66.0 x 85.1 mm, 66 parts (54 on the bottom side), 50 nets.

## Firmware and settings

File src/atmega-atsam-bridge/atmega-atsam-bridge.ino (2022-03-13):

#include <Pololu3piPlus32U4.h>

using namespace Pololu3piPlus32U4;

void setup() {
  Serial1.begin(115200);
  Serial.begin(115200);
  while (!Serial);
}

void loop() {
  if (Serial1.available()) {
    Serial.write(Serial1.read());
  }
  if (Serial.available()) {
    Serial1.write(Serial.read());
  }
}

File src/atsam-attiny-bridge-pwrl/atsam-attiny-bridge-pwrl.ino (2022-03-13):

/*
   Board: Adafruit Feather M0
   Comment on `variants.cpp`:
   `Uart Serial5( &sercom5, PIN_SERIAL_RX, PIN_SERIAL_TX, PAD_SERIAL_RX, PAD_SERIAL_TX ) ;`
   ```
   void SERCOM5_Handler()
   {
     Serial5.IrqHandler();
   }
   ```
*/

#include "wiring_private.h"

Uart mySerial (&sercom5, 6, A5, SERCOM_RX_PAD_2, UART_TX_PAD_0); // Create the new UART instance assigning it to pin 1 and 0

void setup() {
  pinMode(6, OUTPUT);
  digitalWrite(6, HIGH);
  Serial.begin(115200);
  while (!Serial);
  Serial.println("Bridge open");
  digitalWrite(6, LOW);
  delayMicroseconds(750);
  noInterrupts();
  digitalWrite(6, HIGH);
  delayMicroseconds(50);
  digitalWrite(6, LOW);
  interrupts();
  mySerial.begin(115200);
  pinPeripheral(6, PIO_SERCOM); //Assign RX function to pin 6
  pinPeripheral(A5, PIO_SERCOM); //Assign TX function to pin A5
}

void loop() {
  if (mySerial.available())
    Serial.write(mySerial.read());
}

void SERCOM5_Handler() {
  mySerial.IrqHandler();
}

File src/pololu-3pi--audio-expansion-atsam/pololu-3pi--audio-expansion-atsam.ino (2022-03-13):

/*******************************************************************************
   %%SECTION_HEADER%%
   This header information is automatically generated by KodeUtils.

   File 'pololu-3pi--audio-expansion-atsam.ino' edited by RileyStarlight, last modified: 2022-03-07.
   This file is part of 'Pololu 3Ppi+ Audio Expansion' package, please see the readme files
   for more information about this file and this package.

   Copyright (C) 2022 by RileyStarlight <riley.garcia@akornsys-rdi.net>
   Released under the GNU General Public License

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
   %%EOS_HEADER%%
 ******************************************************************************/


/*******************************************************************************
   B O A R D   C O N F I G U R A T I O N
   - MCU: ATSAMD21G18
   - Board: Arduino Zero (Native USB Port)
******************************************************************************/


/*******************************************************************************
    G P I O   C O N S T A N T S
 ******************************************************************************/
#define PWRL                    6                   // PWRL on PA20 (physical pin 29), interlink bidir communication.
#define CS                      10                  // CS on PA18 (physical pin 27), SPI chip select.
#define DEBUG                   13                  // DEBUG on PA17 (physical pin 26), debug LED.
#define AN                      A0                  // AN on PA02 (physical pin 3), unconnected.
//I²S on PA07, PA10 and PA11 (physical pin 12, 15, 16).
//SPI on PA12, PB10 and PB11 (physical pin 21, 19, 20).
// Other pins are unused.

/*******************************************************************************
    A P I   C O N S T A N T S
 ******************************************************************************/
#define PWRL_PRE_US             750                 // Microseconds waiting time between pulses.
#define PWRL_PULSE_US           50                  // Microseconds interlink pulse duration.
#define CHECK_ERROR             '#'                 // Initial check error (ATSAMD21 to ATmega32U4).
#define CHECK_OK                '%'                 // Initial check ok (ATSAMD21 to ATmega32U4).
#define ID_REQUEST              '@'                 // Request identifier (ATmega32U4 to ATSAMD21).
#define ID_ANSWER_UNKNOWN       '@'                 // Answer: Unknown identifier (ATSAMD21 to ATmega32U4).
#define ID_ANSWER_FIRST         'A'                 // Answer: Minimum identifier number (ATSAMD21 to ATmega32U4).
#define ID_ANSWER_LAST          '~'                 // Answer: Maximum identifier number (ATSAMD21 to ATmega32U4).
#define REMOTE_PAUSE            '$'                 // Set pause mode (ATSAMD21 to ATmega32U4).
#define REMOTE_RESUME           '&'                 // Set active mode (ATSAMD21 to ATmega32U4).
#define PLAY_A_FILE             '>'                 // Start of A-Type audio playback (ATmega32U4 to ATSAMD21).
#define STOP_A_FILE             '='                 // End of A-Type audio playback (ATmega32U4 to ATSAMD21).
#define PLAY_B_FILE             '!'                 // Start of B-Type audio playback (ATmega32U4 to ATSAMD21).
#define LOW_BATT                '-'                 // Low battery indicator (ATmega32U4 to ATSAMD21).


/*******************************************************************************
    D E F A U L T   C O N S T A N T S
 ******************************************************************************/
#define N_ROBOTS                5                   // Maximum number of simultaneously active robots.
#define VOLUME                  70                  // Playback volume (0-100).
#define USB_DEBUG               false               // If true use usb debugging.
#define PWRL_PULSE_THRESHOLD    5                   // Microsecond threshold for detection of the pulse sent by ATtiny85.
#define PLAY_MIN_REPETITION     1                   // Minimum number of repetitions of A-Type audios.
#define PLAY_MAX_REPETITION     5                   // Maximum number of repetitions of A-Type audios.


/*******************************************************************************
    P L A Y T Y P E   C O N S T A N T S
 ******************************************************************************/
#define PLAY_NONE               0                   // No file in playback. For use with the `type_playing` variable.
#define PLAY_ATYPE              1                   // A-Type playback. For use with the `type_playing` variable.
#define PLAY_BTYPE              2                   // B-Type playback. For use with the `type_playing` variable.
#define PLAY_SPECIAL            3                   // Special playback. For use with the `type_playing` variable.


/*******************************************************************************
    L I B R A R I E S
 ******************************************************************************/
#include <SD.h>

#include <ArduinoSound.h>
SDWaveFile wave_file;

#include <SDConfig.h>
const char config_file[] = "MAIN.CFG";

void setup() {
  pinMode(PWRL, OUTPUT);
  pinMode(CS, OUTPUT);
  pinMode(DEBUG, OUTPUT);
  randomSeed(analogRead(AN));
  Serial.begin(115200);
  SerialUSB.begin(115200);
  //while (!SerialUSB);
}
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

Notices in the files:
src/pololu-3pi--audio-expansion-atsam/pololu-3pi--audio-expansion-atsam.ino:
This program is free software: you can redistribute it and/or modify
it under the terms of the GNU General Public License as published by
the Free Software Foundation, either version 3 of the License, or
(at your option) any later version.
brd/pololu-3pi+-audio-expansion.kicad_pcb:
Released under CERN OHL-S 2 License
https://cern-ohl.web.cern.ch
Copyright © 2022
